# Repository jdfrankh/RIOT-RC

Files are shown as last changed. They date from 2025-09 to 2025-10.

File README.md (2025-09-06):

### RIOT-RC
This library contains hardware and software files for Robo RIOT's Rc controllers. These sets are meant to control 1lb, 3lb, and possibly 5lb robotics in a compact package, allowing any individual to easily create their own open-source battle bot electronics set.  

## Quickstart -- Preassembled Remote and Receiver

The RIOT RC has the following basic specs

# Receiver
| Parameter | Value |
|---|---|
| Supply Voltage  | 5V - 36V  |
| Idle Amperage Time  | .05A  |
| Default ESC Hookups | 2 |
| Default Servo Hookups | 2 |
| DC Drives | 2 |

# Remote 
| Parameter | Value |
|---|---|
| Operating Time | ~3 hours  |
| Radio Range  | ~40-60m  |
| Analog Joysticks | 2 |
| Buttons | 4 |

# Hookup

The pinout of the Receiver is the following:

Screenshot 2025-09-06 at 12 33 19 AM

Attach your receiver as according to the diagram:

Screenshot 2025-09-06 at 1 02 53 AM

# Basic Operation

The staring operation of the remote goes as such.

1. Start your remote
2. Select your desired reciever by username
3. Control your reciever

The controls for selecting your receiver go as such:

Screenshot 2025-09-06 at 1 23 56 AM

The OLED screen will display all **Powered** receivers automatically with their assigned name. Select one to automatically connect it. 

The controls for the remote after the reciver go as such: 

Screenshot 2025-09-06 at 1 29 56 AM

Keep in mind that there is a **Software** based arming mechanism for the BLDC motor. The receiver will not activate it unless the arming command is first sent. It may take about 5 seconds to arm your receiver. **Please be cautious when actiavate the BLDC, as it's speed rating may be enough to harm.**

The brushed motors are programmed to act as a drive, moving according to a two wheeled battlebot. Although the supply voltage is attached to the motor drive, the original code is deisgned around a 6V N20, and thus creates a PWM signal to prevent users from frying the motor. To change this. Please refer to the **Change code** section for more information.

## Simple edits - Uploading Sketches

Many values as of right now are hard-coded into the remote or receiver to change, and most of those changes can be altered by re-flashing them. The software was created in PlatoformIO, and integrated IDE into VSCode for microcontrollers. Many resources are avaliable for you to download and operate the software.

Once PlatformIO has been downloaded, clone the repository and naviage to /RIOT-RC/PlatformIO Imports/ and select the platoformIO directory. 

**Caution**: The receiver is attached to the battery voltage. **FOR THE RECEIVER DO NOT ATTACH A USB WHILE A LIPO BATTERY IS ATTACHED. YOU WILL FRY YOUR USB PORT AND YOUR COMPUTER**

Most easily accessible commands will be placed at the top of main.cpp for ease of access. Alterations from the basic control scheme will be implemented later. 

Screenshot 2025-09-06 at 1 55 30 AM

# Battery Charging

The Remote has a one cell battery charger. Simply attach the charger to your USB to recharge it.

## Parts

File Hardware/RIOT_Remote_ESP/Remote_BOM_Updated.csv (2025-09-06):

Value | Reference | Footprint | Digikey Link to Item | Qty
MCP73831-2-OT | U9 | Package_TO_SOT_SMD:SOT-23-5 | https://www.digikey.com/en/products/filter/battery-chargers/781?s=N4IgTCBcDaILIGEAKB2AzADjQRhAXQF8g | 1
ASV-40MHz | X1 | Oscillator:Oscillator_SMD_Abracon_ASE-4Pin_3.2x2.5mm_HandSoldering | https://www.digikey.com/en/products/detail/kyocera-avx/CX3225SA40000D0PTWCC/9698138 | 1
TPS63031DSK | U3 | Package_SON:WSON-10-1EP_2.5x2.5mm_P0.5mm_EP1.2x2mm | https://www.digikey.com/en/products/detail/texas-instruments/TPS63031DSKR/2048021 | 1
ESP32-C3FH | U1 | Package_DFN_QFN:QFN-32-1EP_5x5mm_P0.5mm_EP3.7x3.7mm | https://www.digikey.com/en/products/detail/espressif-systems/ESP32-C3FH4X/24366489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 | 1
SM6T10A | D1 | Diode_SMD:D_SMB | https://www.digikey.com/en/products/detail/stmicroelectronics/SM6T10A/1039070 | 1
USB_C_Receptacle_USB2.0_16P | J2 | Connector_USB:USB_C_Receptacle_GCT_USB4085 | https://www.digikey.com/en/products/detail/gct/USB4085-GF-A/9859662?s=N4IgTCBcDaIK4GcBGAWADADgKwgLoF8g | 1
Antenna_Shield | AE1 | Connector_Coaxial:U.FL_Molex_MCRF_73412-0110_Vertical | https://www.digikey.com/en/products/detail/hirose-electric-co-ltd/U-FL-R-SMT-1-60/4285475 | 1
12pF | C1,C2 | Capacitor_SMD:C_0402_1005Metric_Pad0.74x0.62mm_HandSolder |  | 2
10uF | C3,C27,C28,C29 | Capacitor_SMD:C_0603_1608Metric_Pad1.08x0.95mm_HandSolder,Capacitor_SMD:C_1206_3216Metric_Pad1.33x1.80mm_HandSolder |  | 4
1uF | C5,C8,C24 | Capacitor_SMD:C_0402_1005Metric_Pad0.74x0.62mm_HandSolder |  | 3
1p2 | C11 | Capacitor_SMD:C_0402_1005Metric_Pad0.74x0.62mm_HandSolder |  | 1
100uF | C13 | Capacitor_SMD:CP_Elec_4x5.4 |  | 1
100nF | C14,C23,C21,C22,C4,C6,C7,C26 | Capacitor_SMD:C_0402_1005Metric_Pad0.74x0.62mm_HandSolder |  | 8
1p6 | C15 | Capacitor_SMD:C_0402_1005Metric_Pad0.74x0.62mm_HandSolder |  | 1
10nF | C16 | Capacitor_SMD:C_0402_1005Metric_Pad0.74x0.62mm_HandSolder |  | 1
4.7uF | C25 | Capacitor_SMD:C_0402_1005Metric_Pad0.74x0.62mm_HandSolder |  | 1
YELLOW | D2 | LED_SMD:LED_1206_3216Metric_Pad1.42x1.75mm_HandSolder |  | 1
24nH | L1 | Inductor_SMD:L_0603_1608Metric_Pad1.05x0.95mm_HandSolder |  | 1
2 nH | L2 | Inductor_SMD:L_0603_1608Metric_Pad1.05x0.95mm_HandSolder |  | 1
2n2 | L3,L4 | Inductor_SMD:L_0603_1608Metric_Pad1.05x0.95mm_HandSolder |  | 2
1.5uH | L5 | Inductor_SMD:L_Coilcraft_LPS3010 |  | 1
470 | R2 | Resistor_SMD:R_0402_1005Metric_Pad0.72x0.64mm_HandSolder |  | 1
2k | R3 | Resistor_SMD:R_0402_1005Metric_Pad0.72x0.64mm_HandSolder |  | 1
10k | R4 | Resistor_SMD:R_0402_1005Metric_Pad0.72x0.64mm_HandSolder |  | 1
5.1k | R14,R15,R5,R6,R7,R8,R12,R13 | Resistor_SMD:R_0402_1005Metric_Pad0.72x0.64mm_HandSolder |  | 8

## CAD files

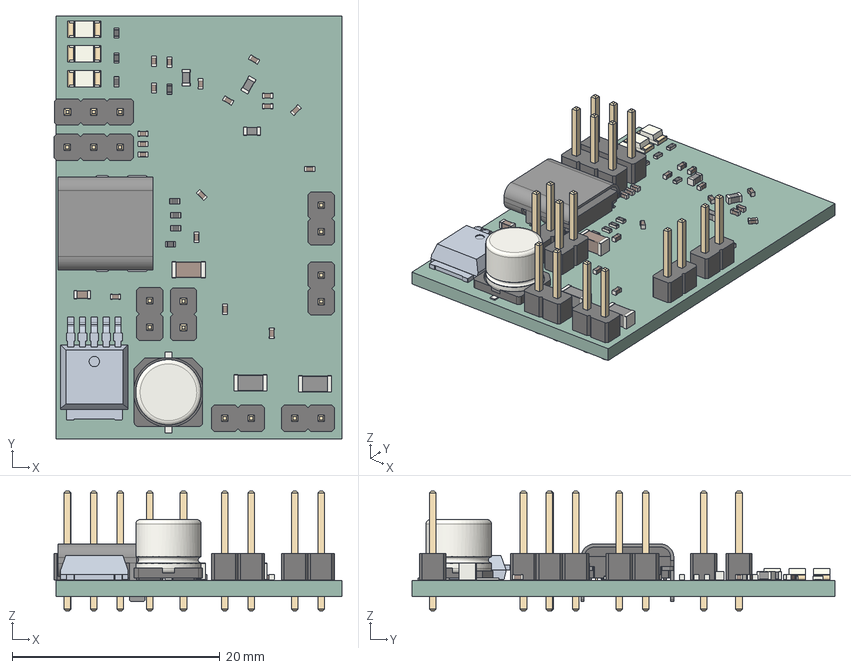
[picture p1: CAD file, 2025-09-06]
CAD/RIOT_Receiver_ESP.step
27.7 x 40.7 x 11.5 mm
PinHeader_1x02_P2.54mm_Vertical x 6
R_0402_1005Metric x 8
LED_1206_3216Metric x 3
C_0402_1005Metric x 18
L_0603_1608Metric x 3
PinHeader_1x03_P2.54mm_Vertical x 2
L_1206_3216Metric x 2
C_Elec_6.3x5.8
C_1206_3216Metric
USB_C_Receptacle_GCT_USB4085
RIOT_Receiver_ESP 1.40.1
C_0603_1608Metric
RIOT_Receiver_ESP_PCB

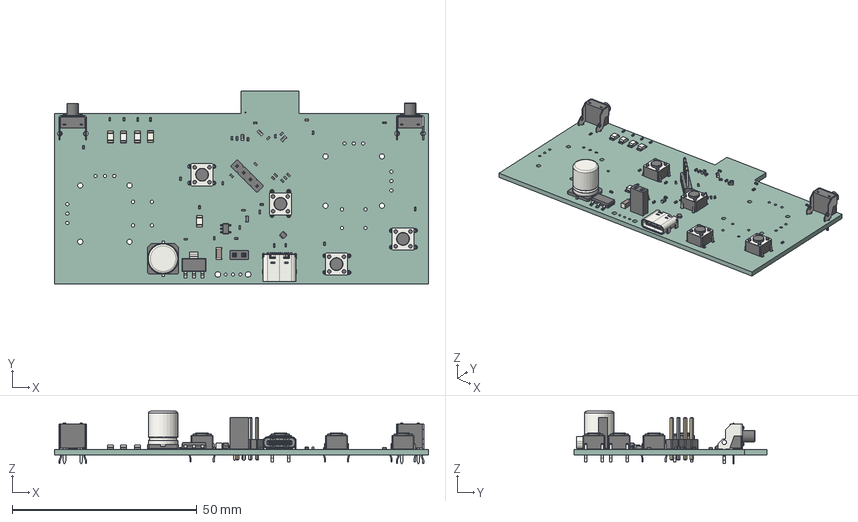
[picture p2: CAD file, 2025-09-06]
Hardware/RIOT_Remote_ESP/RIOT_Remote_ESP.step
101.1 x 52.1 x 14.2 mm
R_0402_1005Metric x 13
USB_C_Receptacle_GCT_USB4105-xx-A_16P_TopMnt_Horizontal
C_0402_1005Metric x 23
L_0603_1608Metric x 4
SOT-666
SW_PUSH_6mm_H4.3mm x 4
LED_1206_3216Metric x 5
PinSocket_1x02_P2.54mm_Vertical
SW_Tactile_SPST_Angled_PTS645Vx58-2LFS x 2
SOT-23-5
C_Elec_8x10.2
SOT-223
C_1206_3216Metric
PinHeader_1x04_P2.54mm_Vertical
RIOT_Remote_ESP_PCB

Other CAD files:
CAD/ESPController v23.f3z

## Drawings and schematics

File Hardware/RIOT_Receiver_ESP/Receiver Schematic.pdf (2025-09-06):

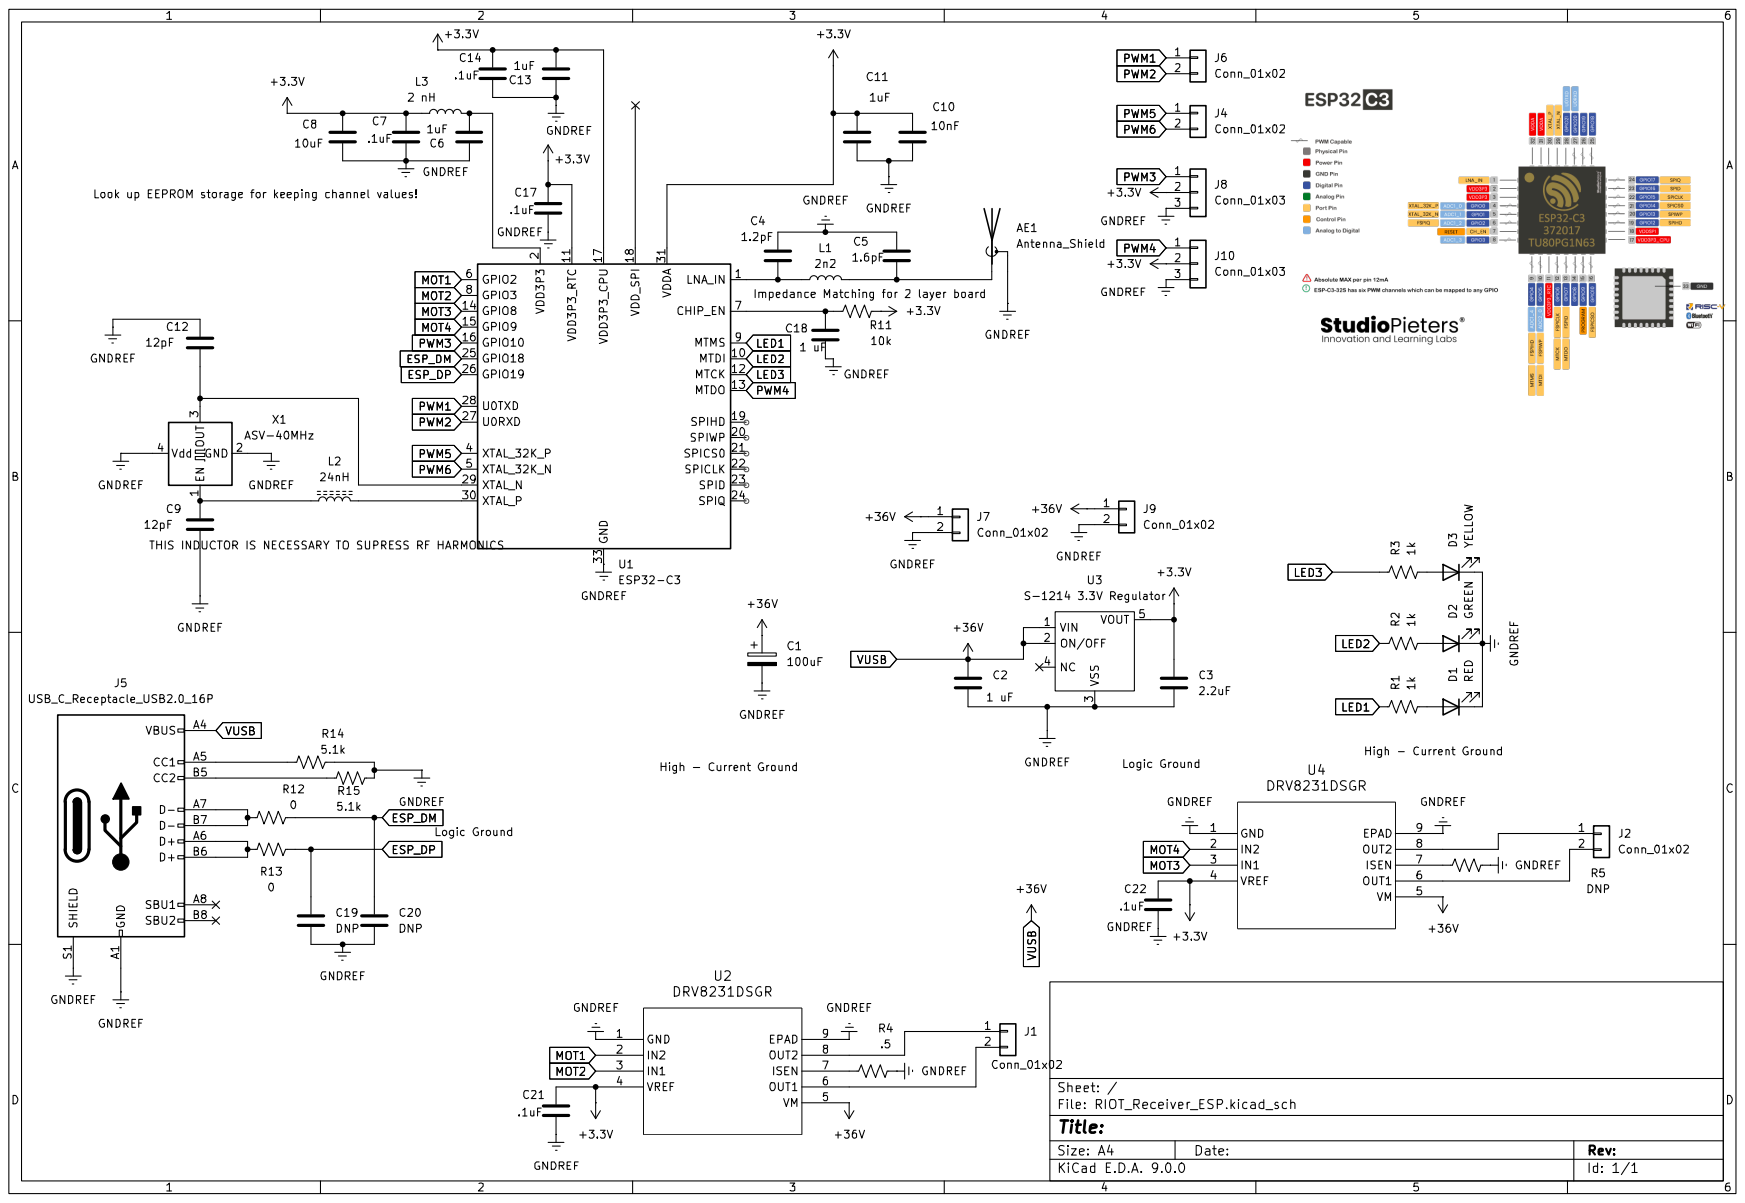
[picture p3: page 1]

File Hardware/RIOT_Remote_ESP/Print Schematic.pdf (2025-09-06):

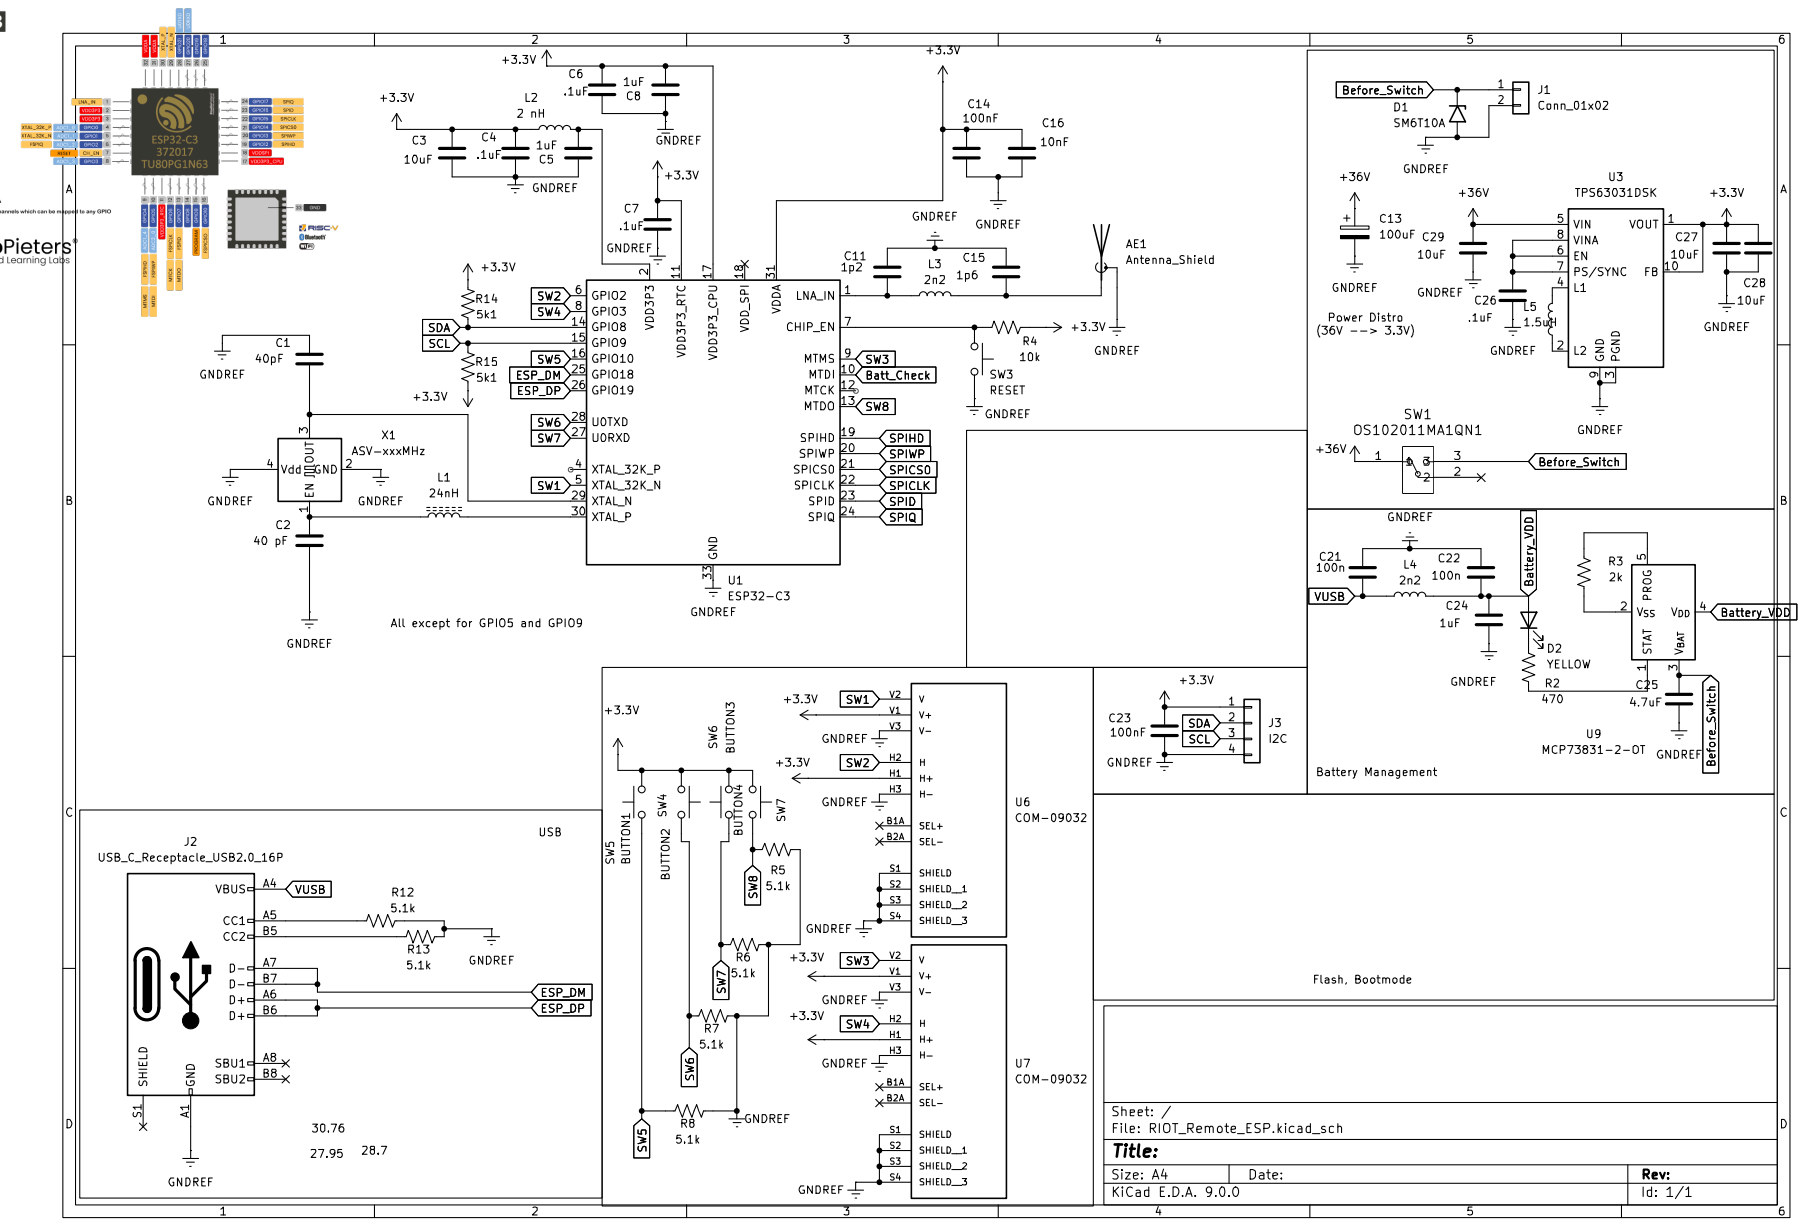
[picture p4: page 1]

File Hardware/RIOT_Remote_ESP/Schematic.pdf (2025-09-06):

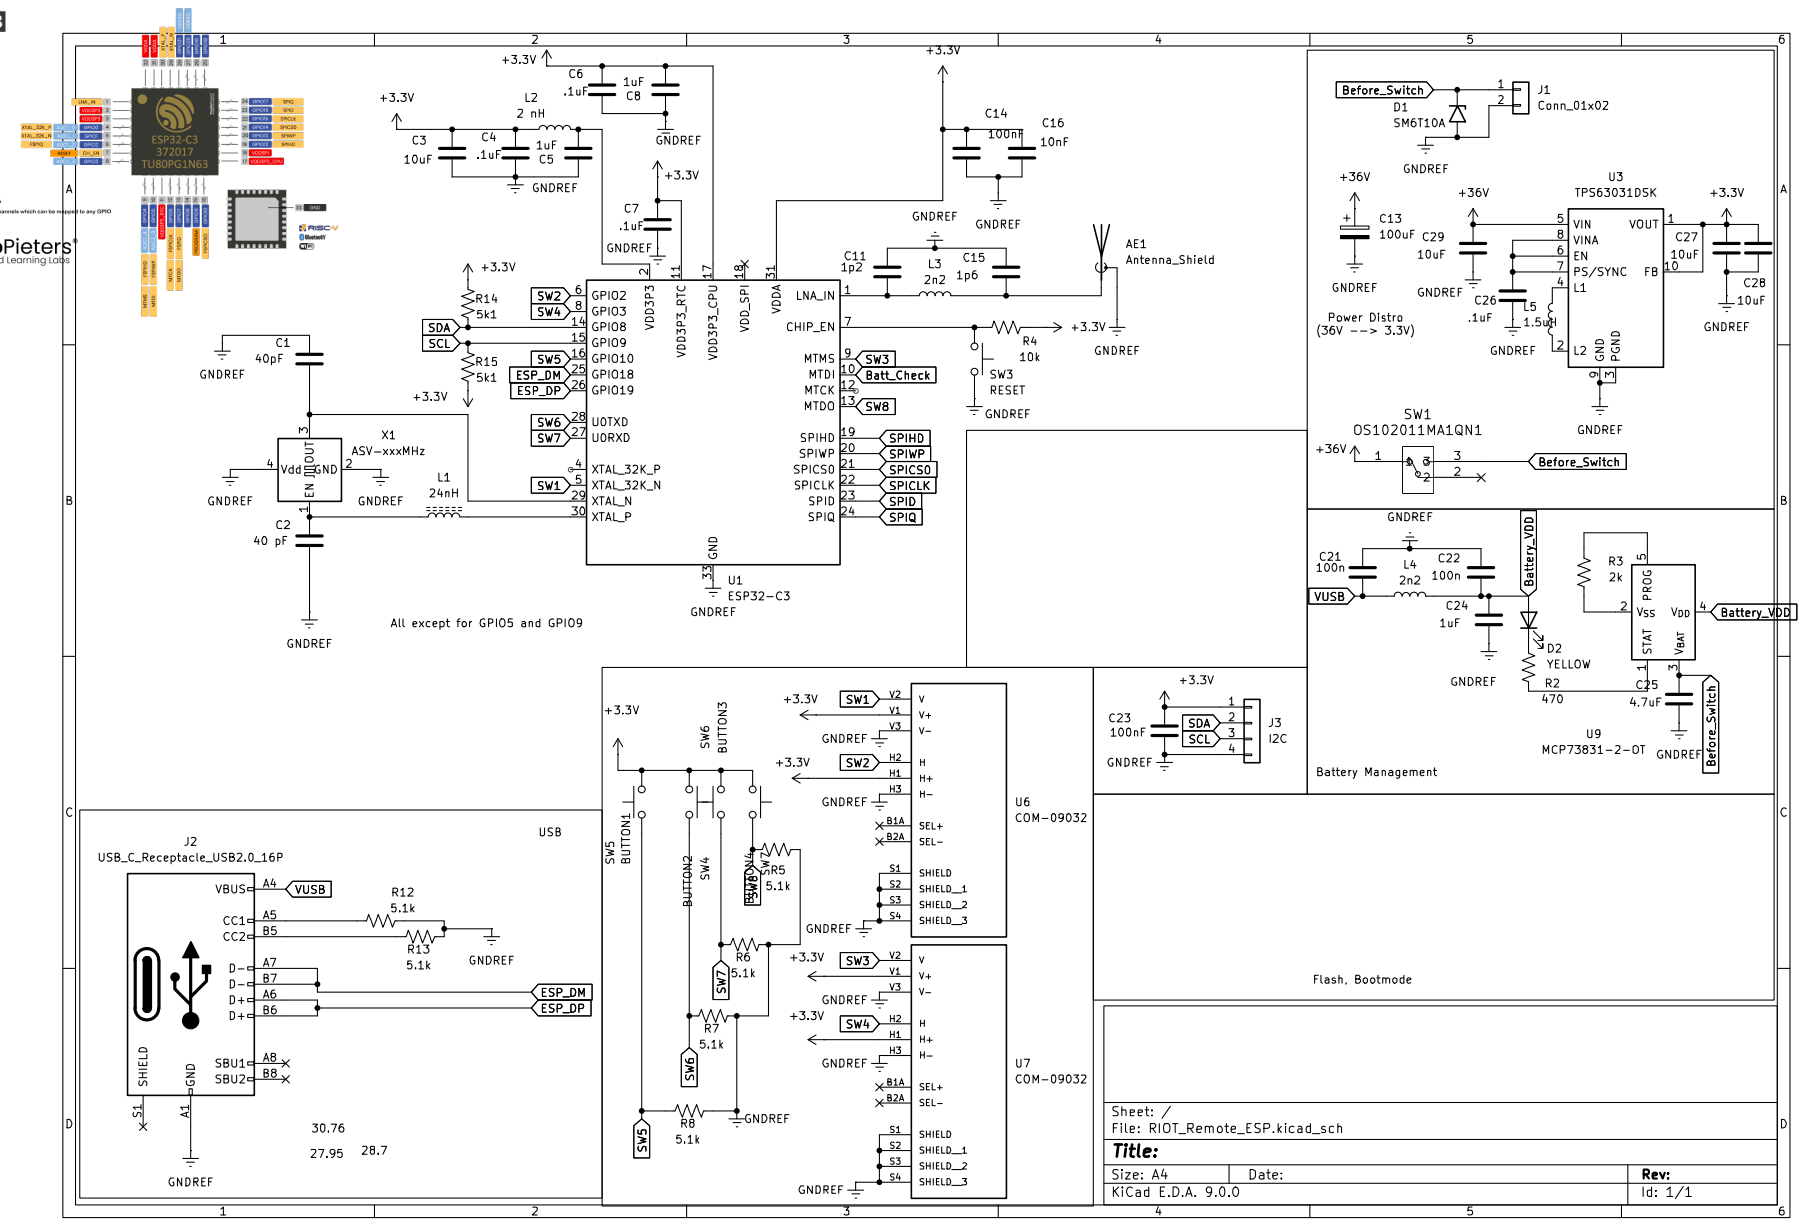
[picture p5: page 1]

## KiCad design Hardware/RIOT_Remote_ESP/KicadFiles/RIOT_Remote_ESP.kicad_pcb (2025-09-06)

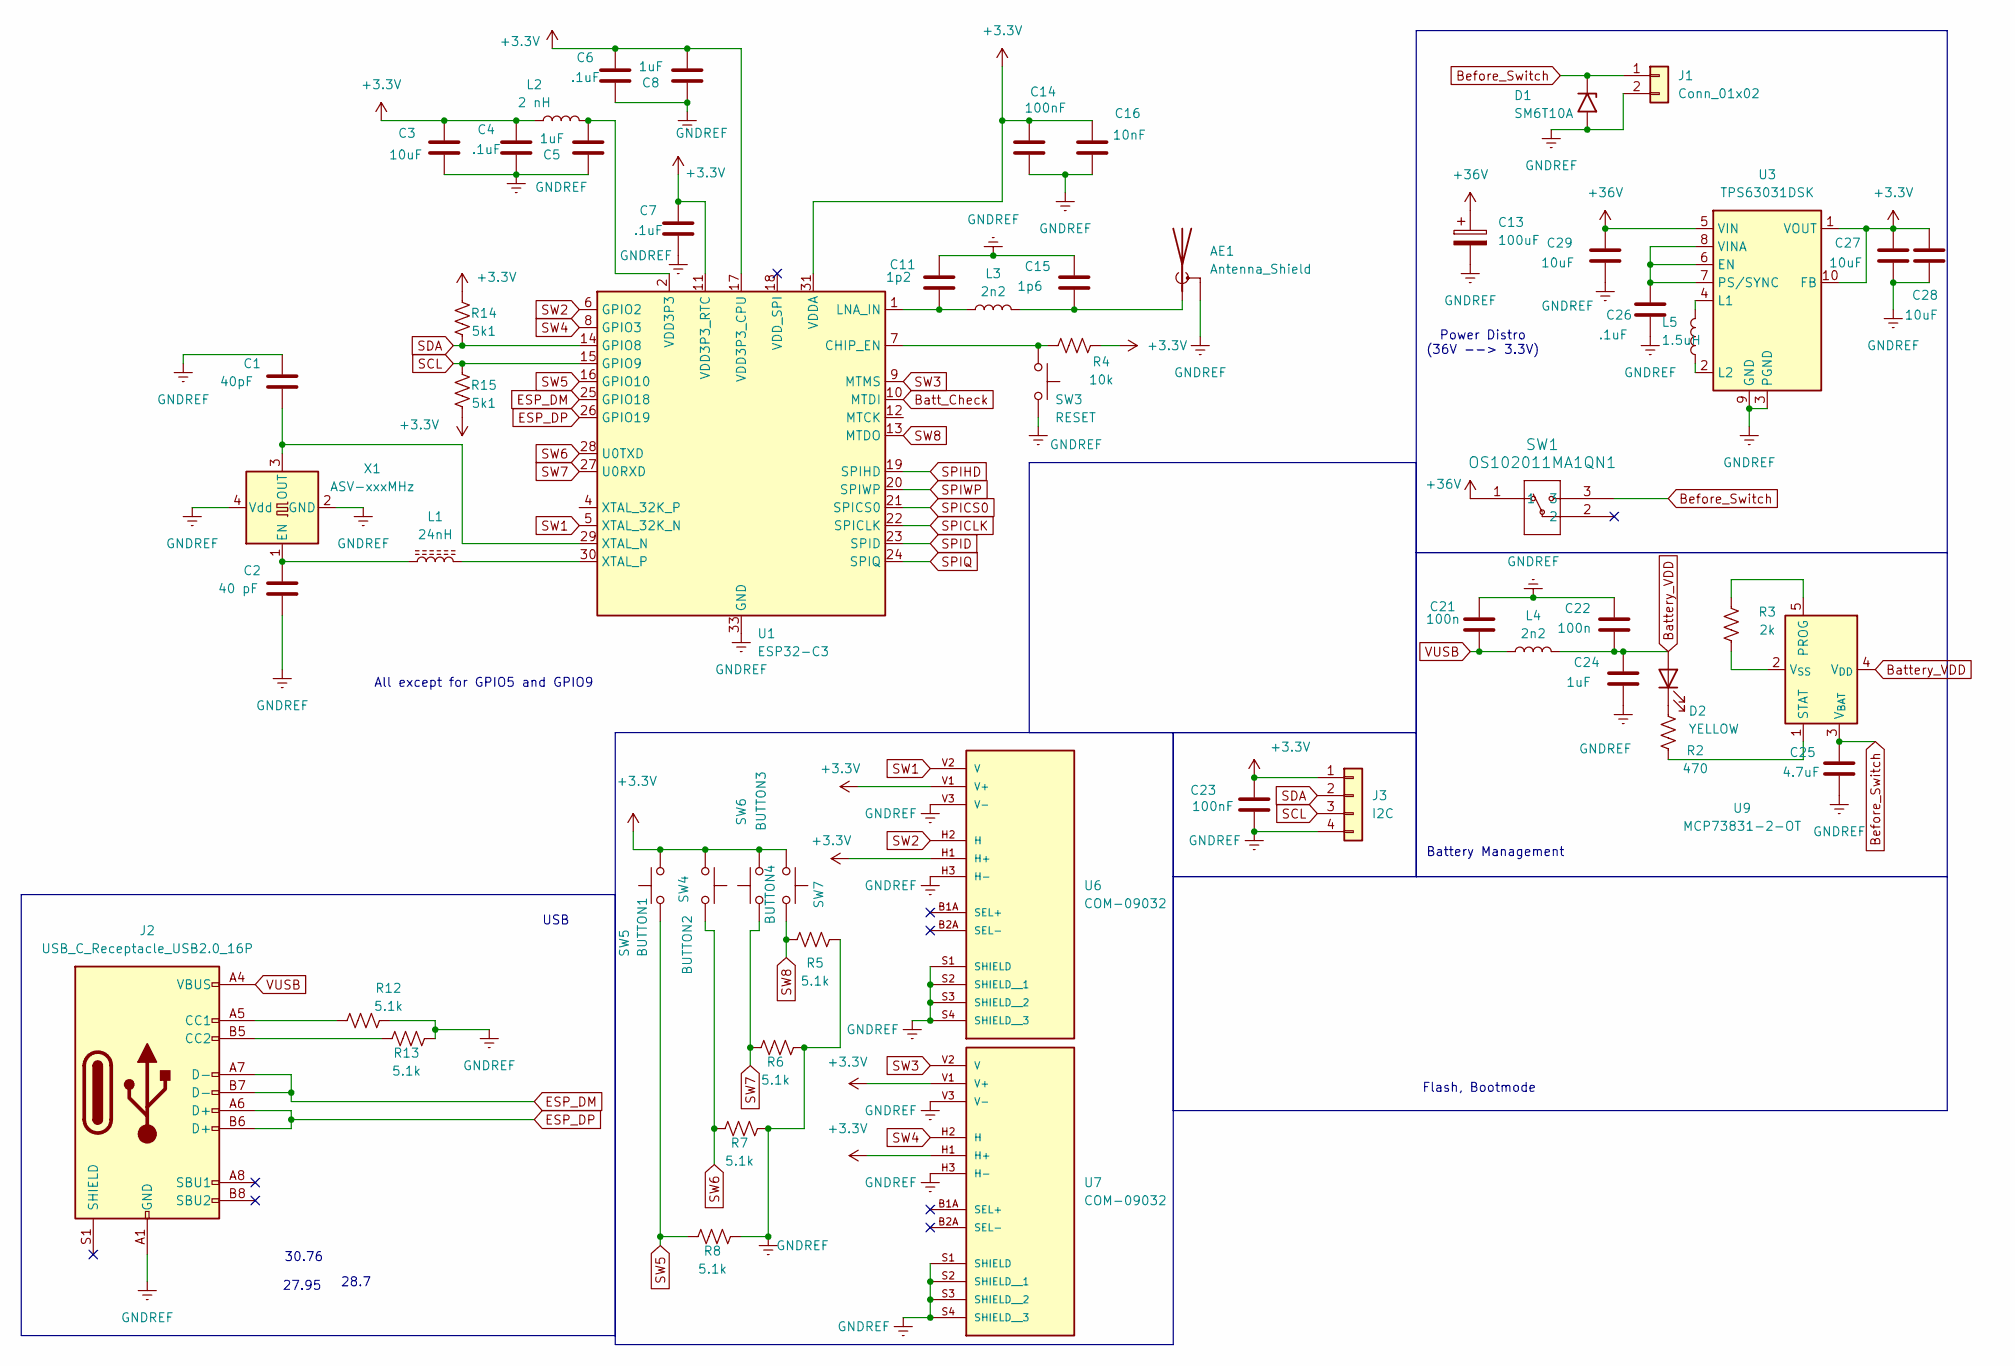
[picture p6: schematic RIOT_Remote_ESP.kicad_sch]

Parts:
AE1: Antenna_Shield; U.FL_Molex_MCRF_73412-0110_Vertical
C1: 40pF; C_0402_1005Metric_Pad0.74x0.62mm_HandSolder
C2: 40 pF; C_0402_1005Metric_Pad0.74x0.62mm_HandSolder
C3: 10uF; C_1206_3216Metric_Pad1.33x1.80mm_HandSolder
C4, C6, C7, C26: .1uF; C_0402_1005Metric_Pad0.74x0.62mm_HandSolder
C5, C8, C24: 1uF; C_0402_1005Metric_Pad0.74x0.62mm_HandSolder
C11: 1p2; C_0402_1005Metric_Pad0.74x0.62mm_HandSolder
C13: 100uF; CP_Elec_4x5.4
C14, C23: 100nF; C_0402_1005Metric_Pad0.74x0.62mm_HandSolder
C15: 1p6; C_0402_1005Metric_Pad0.74x0.62mm_HandSolder
C16: 10nF; C_0402_1005Metric_Pad0.74x0.62mm_HandSolder
C21, C22: 100n; C_0402_1005Metric_Pad0.74x0.62mm_HandSolder
C25: 4.7uF; C_0402_1005Metric_Pad0.74x0.62mm_HandSolder
C27, C28, C29: 10uF; C_0603_1608Metric_Pad1.08x0.95mm_HandSolder
D1: SM6T10A; D_SMB
D2: YELLOW; LED_1206_3216Metric_Pad1.42x1.75mm_HandSolder
J1: Conn_01x02; PinSocket_1x02_P2.54mm_Vertical
J2: USB_C_Receptacle_USB2.0_16P; USB_C_Receptacle_GCT_USB4085
J3: I2C; PinHeader_1x04_P2.54mm_Vertical
L1: 24nH; L_0603_1608Metric_Pad1.05x0.95mm_HandSolder
L2: 2 nH; L_0603_1608Metric_Pad1.05x0.95mm_HandSolder
L3, L4: 2n2; L_0603_1608Metric_Pad1.05x0.95mm_HandSolder
L5: 1.5uH; L_Coilcraft_LPS3010
R2: 470; R_0402_1005Metric_Pad0.72x0.64mm_HandSolder
R3: 2k; R_0402_1005Metric_Pad0.72x0.64mm_HandSolder
R4: 10k; R_0402_1005Metric_Pad0.72x0.64mm_HandSolder
R5, R6, R7, R8, R12, R13: 5.1k; R_0402_1005Metric_Pad0.72x0.64mm_HandSolder
R14, R15: 5k1; R_0402_1005Metric_Pad0.72x0.64mm_HandSolder
SW1: OS102011MA1QN1; OS102011MA1QN1_CNK
SW3: RESET; SW_PUSH_6mm_H4.3mm
SW4: BUTTON2; SW_Tactile_SPST_Angled_PTS645Vx58-2LFS
SW5: BUTTON1; SW_PUSH_6mm_H4.3mm
SW6: BUTTON3; SW_PUSH_6mm_H4.3mm
SW7: BUTTON4; SW_Tactile_SPST_Angled_PTS645Vx58-2LFS
U1: ESP32-C3; QFN-32-1EP_5x5mm_P0.5mm_EP3.7x3.7mm
U3: TPS63031DSK; WSON-10-1EP_2.5x2.5mm_P0.5mm_EP1.2x2mm
U6, U7: COM-09032; XDCR_COM-09032; PARTREV N/A
U9: MCP73831-2-OT; SOT-23-5
X1: ASV-xxxMHz; Oscillator_SMD_Abracon_ASE-4Pin_3.2x2.5mm_HandSoldering

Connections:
+3.3V: C3.1, C4.1, C6.1, C7.1, C8.2, C14.1, C16.1, C23.1, C27.1, C28.1, J3.1, L2.1, R4.2, R14.2, R15.1, SW4.1, SW5.2, SW6.2, SW7.1, U1.11 (VDD3P3_RTC), U1.17 (VDD3P3_CPU), U1.31 (VDDA), U1.32 (VDDA), U3.1 (VOUT), U3.10 (FB), U6.H1 (H+), U6.V1 (V+), U7.H1 (H+), U7.V1 (V+)
+36V: C13.1, C29.1, SW1.1, U3.5 (VIN); also elsewhere on the board
Batt_Check: U1.10 (MTDI)
Battery_VDD: C22.2, C24.1, D2.2 (A), L4.2, U9.4 (V_{DD})
Before_Switch: C25.1, D1.1 (A1), J1.1, SW1.3, U9.3 (V_{BAT}); also elsewhere on the board
ESP_DM: J2.A7 (D-), J2.B7 (D-), U1.25 (GPIO18)
ESP_DP: J2.A6 (D+), J2.B6 (D+), U1.26 (GPIO19)
GNDREF: AE1.2 (Shield), C1.1, C2.2, C3.2, C4.2, C5.1, C6.2, C7.2, C8.1, C11.1, C13.2, C14.2, C15.1, C16.2, C21.1, C22.1, C23.2, C24.2, C25.2, C26.2, C27.2, C28.2, C29.2, D1.2 (A2), J1.2, J2.A1 (GND), J2.A12 (GND), J2.B1 (GND), J2.B12 (GND), J3.4, R5.2, R6.2, R7.2, R8.2, R12.2, R13.2, SW3.2, U1.33 (GND), U3.3 (PGND), U3.9 (GND), U3.11 (PGND), U6.H3 (H-), U6.S1 (SHIELD), U6.S2 (SHIELD__1), U6.S3 (SHIELD__2), U6.S4 (SHIELD__3), U6.V3 (V-), U7.H3 (H-), U7.S1 (SHIELD), U7.S2 (SHIELD__1), U7.S3 (SHIELD__2), U7.S4 (SHIELD__3), U7.V3 (V-), X1.2 (GND), X1.4 (Vdd); also elsewhere on the board
unnamed: AE1.1 (A), C15.2, L3.2
unnamed: C5.2, L2.2, U1.2 (VDD3P3), U1.3 (VDD3P3)
unnamed: D2.1 (K), R2.2
unnamed: J2.A5 (CC1), R12.1
unnamed: J2.B5 (CC2), R13.1
unnamed: R4.1, SW3.1, U1.7 (CHIP_EN)
unnamed: C11.2, L3.1, U1.1 (LNA_IN)
unnamed: C1.2, U1.29 (XTAL_N), X1.3 (OUT)
unnamed: L1.2, U1.30 (XTAL_P)
unnamed: C26.1, U3.6 (EN), U3.7 (PS/SYNC), U3.8 (VINA)
unnamed: L5.2, U3.4 (L1)
unnamed: L5.1, U3.2 (L2)
unnamed: R3.2, U9.5 (PROG)
unnamed: R2.1, U9.1 (STAT)
unnamed: R3.1, U9.2 (V_{SS})
unnamed: C2.1, L1.1, X1.1 (EN)
SCL: J3.3, R15.2, U1.15 (GPIO9)
SDA: J3.2, R14.1, U1.14 (GPIO8)
SPICLK: U1.22 (SPICLK)
SPICS0: U1.21 (SPICS0)
SPID: U1.23 (SPID)
SPIHD: U1.19 (SPIHD)
SPIQ: U1.24 (SPIQ)
SPIWP: U1.20 (SPIWP)
SW1: U1.5 (XTAL_32K_N), U6.V2 (V)
SW2: U1.6 (GPIO2), U6.H2 (H)
SW3: U1.9 (MTMS), U7.V2 (V)
SW4: U1.8 (GPIO3), U7.H2 (H)
SW5: R8.1, SW5.1, U1.16 (GPIO10)
SW6: R7.1, SW4.2, U1.28 (U0TXD)
SW7: R6.1, SW6.1, U1.27 (U0RXD)
SW8: R5.1, SW7.2, U1.13 (MTDO)
VUSB: C21.2, J2.A4 (VBUS), J2.A9 (VBUS), J2.B4 (VBUS), J2.B9 (VBUS), L4.1

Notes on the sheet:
28.7
Battery Management
Power Distro (36V --> 3.3V)
Flash, Bootmode
27.95
All except for GPIO5 and GPIO9
USB
30.76

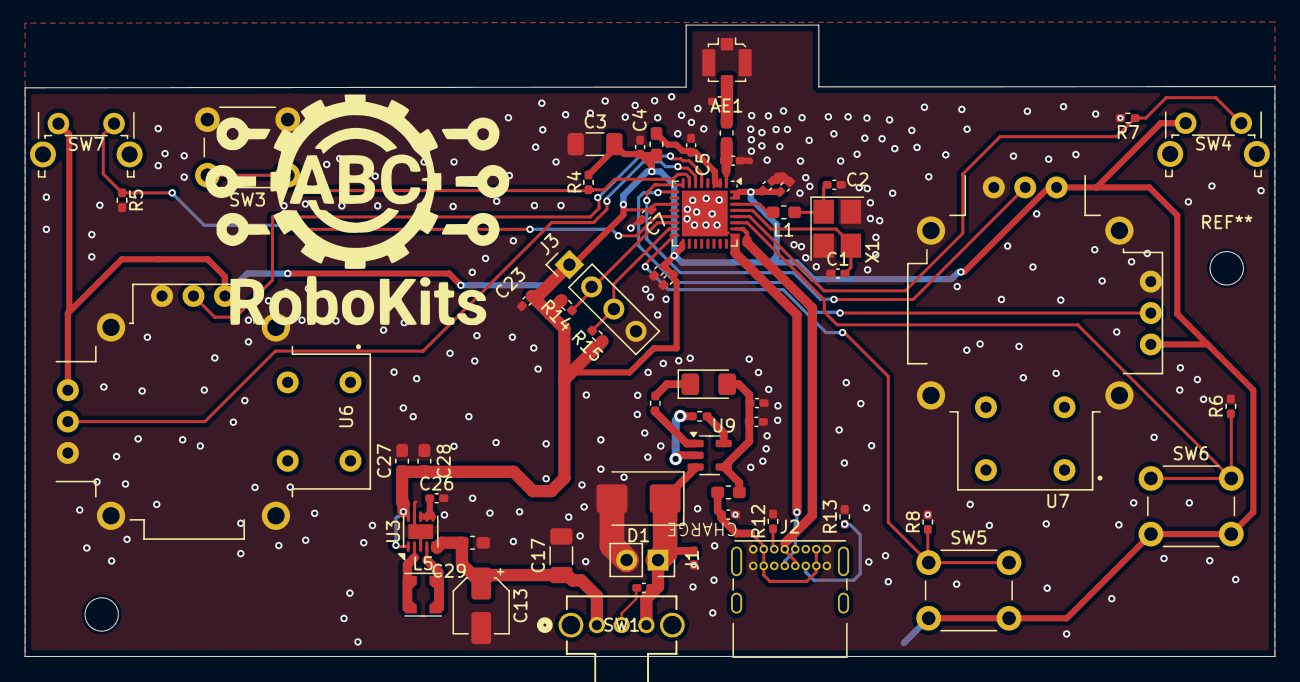
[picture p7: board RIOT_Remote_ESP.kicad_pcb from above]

Board: 2 copper layers, 101.1 x 51.1 mm, 58 parts (0 on the bottom side), 34 nets.

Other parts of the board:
C17: 1 uF; C_1206_3216Metric_Pad1.33x1.80mm_HandSolder
C25#2: 4.7uF; C_0402_1005Metric_Pad0.74x0.62mm_HandSolder

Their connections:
+36V: C17.1; also elsewhere on the board
Before_Switch: C25#2.1; also elsewhere on the board
GNDREF: C17.2, C25#2.2; also elsewhere on the board

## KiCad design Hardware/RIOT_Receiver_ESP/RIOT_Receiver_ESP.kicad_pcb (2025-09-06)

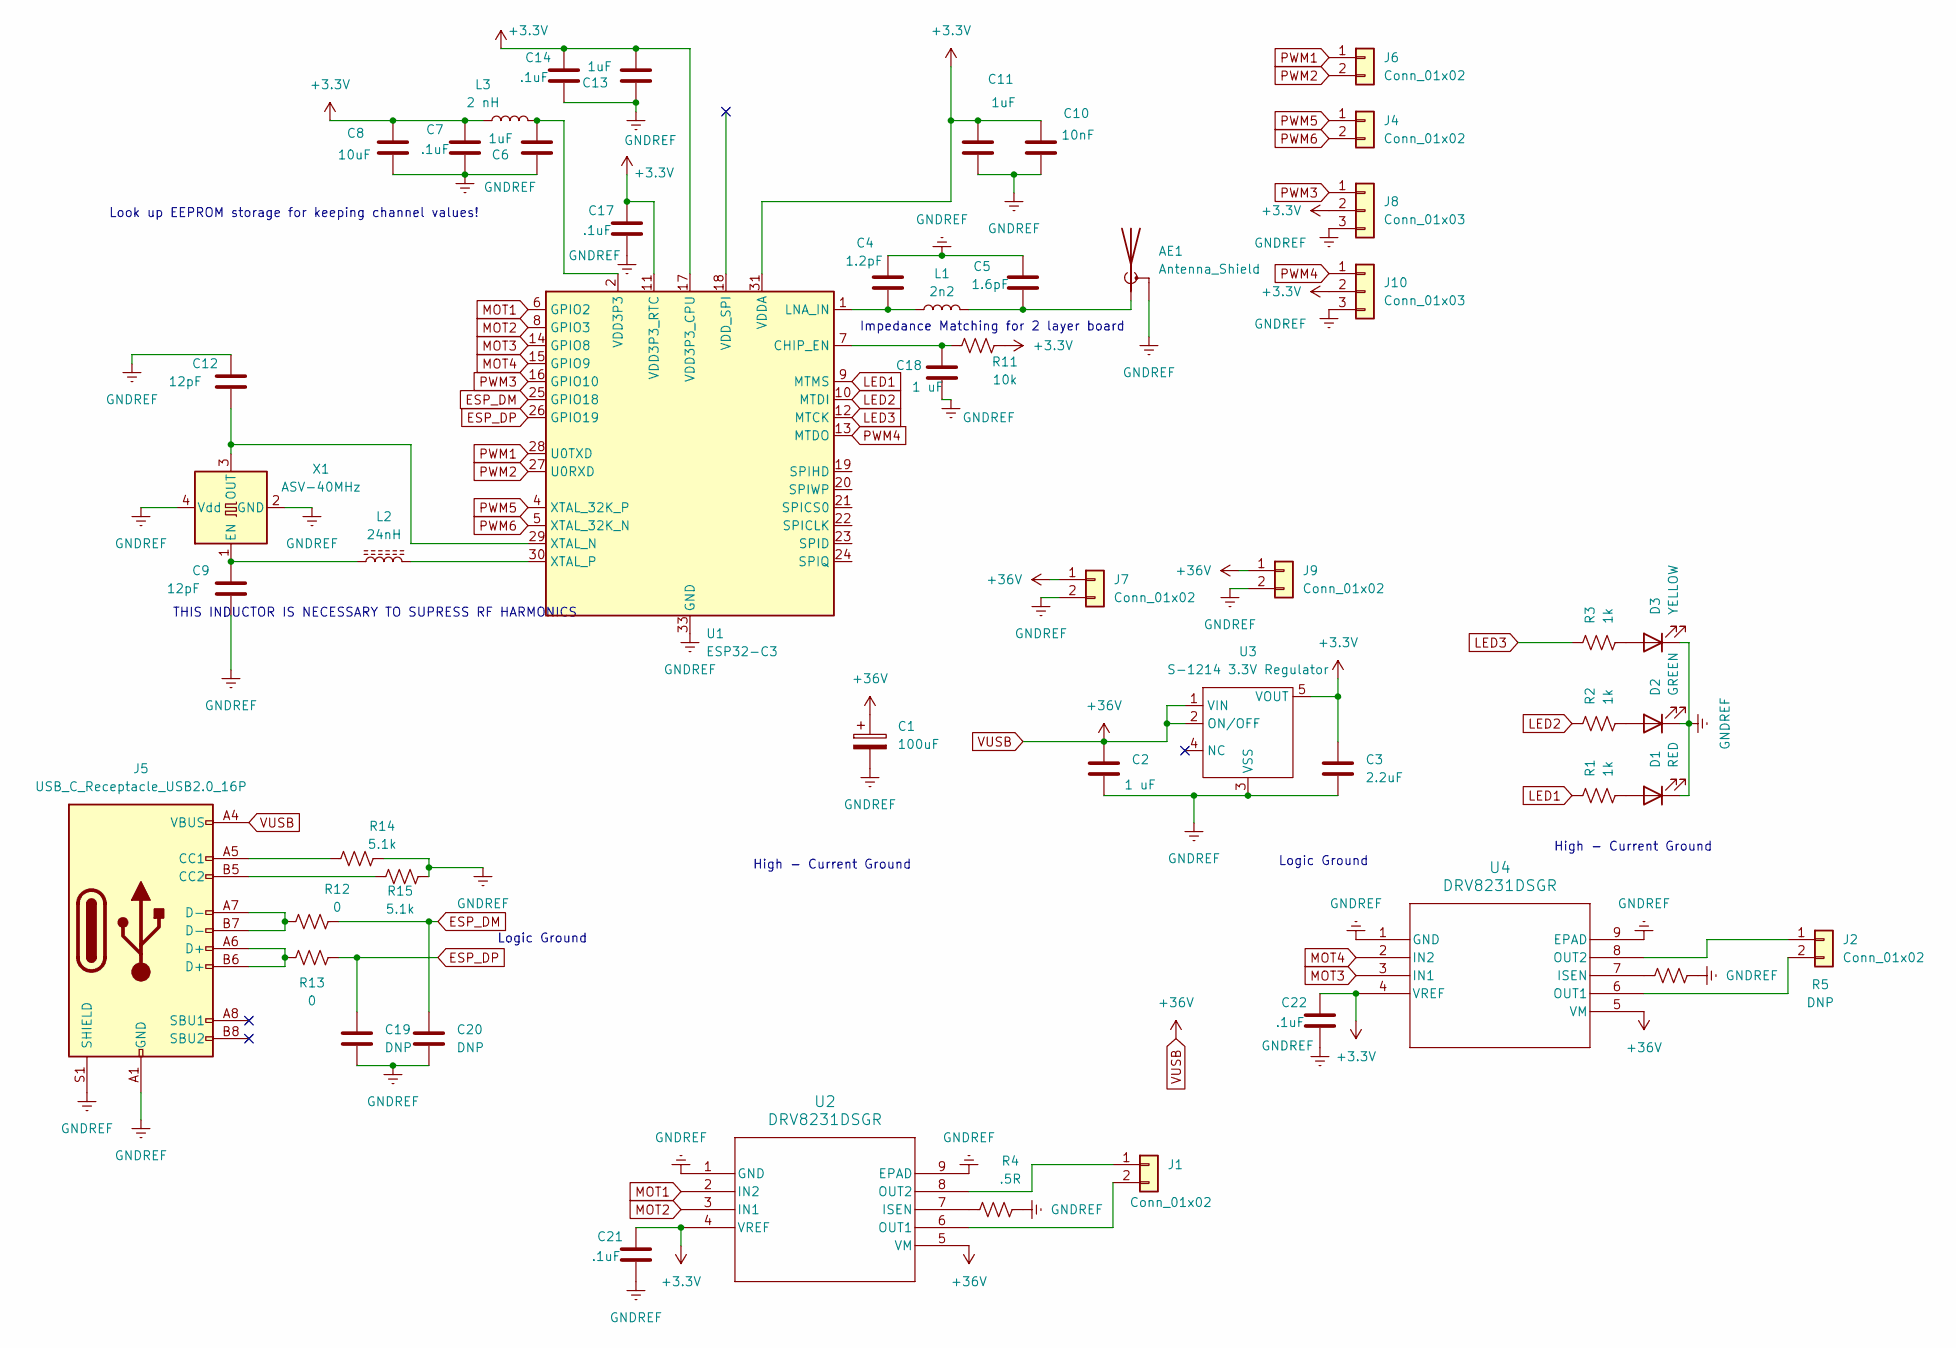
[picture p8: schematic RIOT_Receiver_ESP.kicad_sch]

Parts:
AE1: Antenna_Shield
C1: 100uF; C_Elec_8x10.2
C2, C18: 1 uF; C_0402_1005Metric_Pad0.74x0.62mm_HandSolder
C3: 2.2uF; C_0603_1608Metric_Pad1.08x0.95mm_HandSolder
C4: 1.2pF; C_0402_1005Metric_Pad0.74x0.62mm_HandSolder
C5: 1.6pF; C_0402_1005Metric_Pad0.74x0.62mm_HandSolder
C6, C11, C13: 1uF; C_0402_1005Metric_Pad0.74x0.62mm_HandSolder
C7, C14, C17, C21, C22: .1uF; C_0402_1005Metric_Pad0.74x0.62mm_HandSolder
C8: 10uF; C_0402_1005Metric_Pad0.74x0.62mm_HandSolder
C9, C12: 12pF; C_0402_1005Metric_Pad0.74x0.62mm_HandSolder
C10: 10nF; C_0402_1005Metric_Pad0.74x0.62mm_HandSolder
C19, C20: DNP; C_0402_1005Metric_Pad0.74x0.62mm_HandSolder
D1: RED; LED_1206_3216Metric_Pad1.42x1.75mm_HandSolder
D2: GREEN; LED_1206_3216Metric_Pad1.42x1.75mm_HandSolder
D3: YELLOW; LED_1206_3216Metric_Pad1.42x1.75mm_HandSolder
J1, J2, J4, J6, J7, J9: Conn_01x02; PinHeader_1x02_P2.54mm_Vertical
J5: USB_C_Receptacle_USB2.0_16P; USB_C_Receptacle_GCT_USB4085
J8, J10: Conn_01x03; PinHeader_1x03_P2.54mm_Vertical
L1: 2n2; L_0603_1608Metric_Pad1.05x0.95mm_HandSolder
L2: 24nH; L_0603_1608Metric_Pad1.05x0.95mm_HandSolder
L3: 2 nH; L_0603_1608Metric_Pad1.05x0.95mm_HandSolder
R1, R2, R3: 1k; R_0402_1005Metric_Pad0.72x0.64mm_HandSolder
R4: .5R; L_1206_3216Metric_Pad1.22x1.90mm_HandSolder
R5: DNP; L_1206_3216Metric_Pad1.22x1.90mm_HandSolder
R11: 10k; R_0402_1005Metric_Pad0.72x0.64mm_HandSolder
R12, R13: 0; R_0402_1005Metric_Pad0.72x0.64mm_HandSolder
R14, R15: 5.1k; R_0402_1005Metric_Pad0.72x0.64mm_HandSolder
U1: ESP32-C3; QFN-32-1EP_5x5mm_P0.5mm_EP3.7x3.7mm
U2, U4: DRV8231DSGR; WSON8_DRV8231_TEX
U3: S-1214 3.3V Regulator; TO-252-5_TabPin3
X1: ASV-40MHz; Oscillator_SMD_Abracon_ASE-4Pin_3.2x2.5mm

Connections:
+3.3V: C3.1, C7.1, C8.1, C10.1, C11.1, C13.2, C14.1, C17.1, C21.1, C22.1, J8.2, J10.2, L3.1, R11.2, U1.11 (VDD3P3_RTC), U1.17 (VDD3P3_CPU), U1.31 (VDDA), U1.32 (VDDA), U2.4 (VREF), U3.5 (VOUT), U4.4 (VREF)
ESP_DM: C20.1, R12.2, U1.25 (GPIO18)
ESP_DP: C19.1, R13.1, U1.26 (GPIO19)
GNDREF: AE1.2 (Shield), C1.2, C2.2, C3.2, C4.1, C5.1, C6.1, C7.2, C8.2, C9.2, C10.2, C11.2, C12.1, C13.1, C14.2, C17.2, C18.2, C19.2, C20.2, C21.2, C22.2, D1.1 (K), D2.1 (K), D3.1 (K), J5.A1 (GND), J5.A12 (GND), J5.B1 (GND), J5.B12 (GND), J5.S1 (SHIELD), J7.2, J8.3, J9.2, J10.3, R4.2, R5.2, R14.2, R15.2, U1.33 (GND), U2.1 (GND), U2.9 (EPAD), U3.3 (VSS), U4.1 (GND), U4.9 (EPAD), X1.2 (GND), X1.4 (Vdd)
LED1: R1.1, U1.9 (MTMS)
LED2: R2.1, U1.10 (MTDI)
LED3: R3.1, U1.12 (MTCK)
MOT1: U1.6 (GPIO2), U2.2 (IN2)
MOT2: U1.8 (GPIO3), U2.3 (IN1)
MOT3: U1.14 (GPIO8), U4.3 (IN1)
MOT4: U1.15 (GPIO9), U4.2 (IN2)
unnamed: AE1.1 (A), C5.2, L1.2
unnamed: C6.2, L3.2, U1.2 (VDD3P3), U1.3 (VDD3P3)
unnamed: D1.2 (A), R1.2
unnamed: D2.2 (A), R2.2
unnamed: D3.2 (A), R3.2
unnamed: J1.1, U2.8 (OUT2)
unnamed: J1.2, U2.6 (OUT1)
unnamed: J2.1, U4.8 (OUT2)
unnamed: J2.2, U4.6 (OUT1)
unnamed: J5.A5 (CC1), R14.1
unnamed: J5.B5 (CC2), R15.1
unnamed: J5.A6 (D+), J5.B6 (D+), R13.2
unnamed: J5.A7 (D-), J5.B7 (D-), R12.1
unnamed: C18.1, R11.1, U1.7 (CHIP_EN)
unnamed: C4.2, L1.1, U1.1 (LNA_IN)
unnamed: C12.2, U1.29 (XTAL_N), X1.3 (OUT)
unnamed: L2.2, U1.30 (XTAL_P)
unnamed: R4.1, U2.7 (ISEN)
unnamed: R5.1, U4.7 (ISEN)
unnamed: C9.1, L2.1, X1.1 (EN)
PWM1: J6.1, U1.28 (U0TXD)
PWM2: J6.2, U1.27 (U0RXD)
PWM3: J8.1, U1.16 (GPIO10)
PWM4: J10.1, U1.13 (MTDO)
PWM5: J4.1, U1.4 (XTAL_32K_P)
PWM6: J4.2, U1.5 (XTAL_32K_N)
VUSB: C1.1, C2.1, J5.A4 (VBUS), J5.A9 (VBUS), J5.B4 (VBUS), J5.B9 (VBUS), J7.1, J9.1, U2.5 (VM), U3.1 (VIN), U3.2 (ON/OFF), U4.5 (VM)

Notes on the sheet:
THIS INDUCTOR IS NECESSARY TO SUPRESS RF HARMONICS
Logic Ground
High - Current Ground
Look up EEPROM storage for keeping channel values!
Impedance Matching for 2 layer board

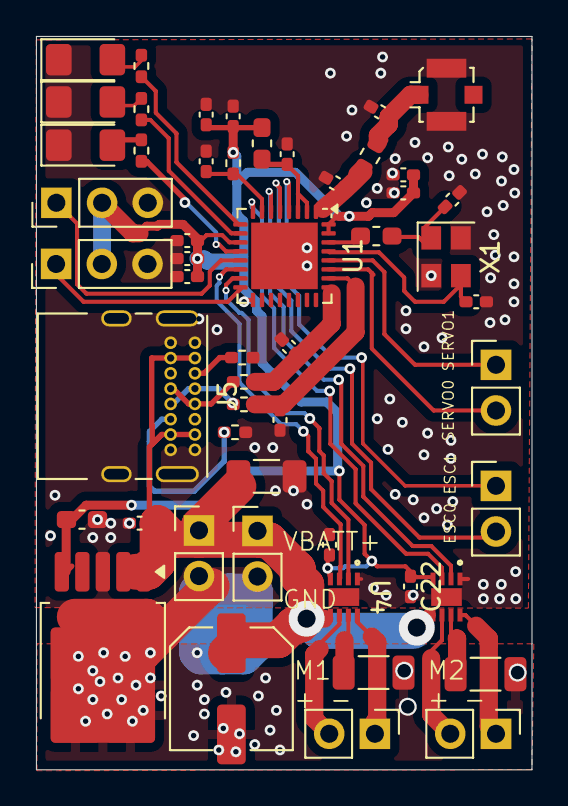
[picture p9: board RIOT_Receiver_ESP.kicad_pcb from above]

Board: 2 copper layers, 27.5 x 40.7 mm, 49 parts (0 on the bottom side), 38 nets.

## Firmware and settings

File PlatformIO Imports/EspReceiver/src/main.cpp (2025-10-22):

#include <Arduino.h>
#include <WiFi.h>
#include "EspNowEZ.h"
#include <esp_now.h>
#include <esp_system.h>
#include "esp_wifi.h"
#include <ESP32Servo.h>
#include <vector>
#include "ESC.h" // RC_ESP library installed by Library Manager

const uint8_t broadcastAddress[] = {0xFF, 0xFF, 0xFF, 0xFF, 0xFF, 0xFF};
int timeout = 0;
bool receivedRemoteSignal = false; 

#define Mot1 2
#define Mot2 3

#define Mot3 8
#define Mot4 9


#define ESC1 0
#define ESC2 1

//Servo library defaults from 20 to 180
#define ESCSMINDISTANCE 1000
#define ESCMAXDISTANCE 1900

#define SERVO1 10
#define SERVO2 7

#define SERVOIDLEANGLE 0
#define SERVOARMANGLE 90
#define SERVOATTACKANGLE 180

#define PWM1 20
#define PWM2 21

#define LED1 4
#define LED2 5
#define LED3 6


Servo FirstESC;
float escSpeed1 = 0;
ESC SecondESC(ESC2, 1000, 2000, 1000); 
uint16_t escSpeed2 = 0;
bool ESCArm[2] = {false, false};





//struct __attribute__((packed)) Message{
  const char id[20] = "Spenc";
//};



struct __attribute__((packed)) sendData{
    uint8_t macHandshake[6];
    uint8_t Direction[2]; // 0,1,2,3 FWD, BWD, Left, Right

    uint8_t DcMax[2] = {255,255};
    uint8_t DcMin[2] = {0,0};
    uint8_t dcMagnitude[2] = {0,0}; //Should be between 0 and 100
    bool objectArm[6]; // For escs, arm them, for servos, set to zero degrees? or fixable value
    bool objectRun[6]; 
    float escSpeed = .25; 

    bool connectCheck = false;
};

Container message;
uint8_t macAddress[6];
//Message msg;
sendData sD;
bool waitingForResponse(){

 

  //message.store(msg); 
  //message.printBytes();
  int result = esp_now_send(broadcastAddress, (uint8_t*) &id, sizeof(id) );
  //int result = ESPNow.broadcastMessage(message);
  result == ESP_OK ? digitalWrite(LED1, !digitalRead(LED1)) : digitalWrite(LED1, LOW);

  result == ESP_OK ? Serial.println("Sent successfully"): Serial.printf("Print failure %02x", ESP_OK);


  delay(250); // Send every 2 seconds


  return(true);

}

// Optional: callback for send status
//void onSend(const uint8_t *mac_addr, esp_now_send_status_t status) {

//}

void onReceive(const esp_now_recv_info *mac_info, const uint8_t *incomingData, int len) {
  const uint8_t *recv_info = mac_info->src_addr;
  
  if (len == sizeof(sendData)) {
    Serial.println("Data received from remote!"); 
    memcpy(&sD, incomingData, sizeof(sendData));

    //Serial.printf("%02x ,%02x,%02x,%20x: ", sD.Direction[0], sD.Direction[1], sD.objectRun[0], sD.objectArm[0]);
  //  for(size_t i= 0; i < len; i++){
  //    Serial.printf("%02X,", incomingData[i]);
  //  }
  //  Serial.printf("Length: %d", len);
  //  Serial.printf(": %d", sD.Direction[0]);
  //  Serial.println();

  //Serial.printf("Arm 0: %d, Arm 1: %d, Interact 0: %d, Interact 1: %d" , sD.objectArm[0],sD.objectArm[1], sD.objectRun[0], sD.objectRun[1] );
  //Serial.println();

    if (!esp_now_is_peer_exist(sD.macHandshake)) {
    Serial.println("Adding peer");
    ESPNow.add_peer(sD.macHandshake);
    }
    
    digitalWrite(LED2, HIGH);
    timeout = 1000;



    if(sD.macHandshake[5] == macAddress[5] && sD.macHandshake[4] == macAddress[4] && sD.macHandshake[3] == macAddress[3] ){
      digitalWrite(LED3, HIGH);
    }

  } else {
    Serial.print("Unexpected message length: ");
    Serial.println(len);
  }


}




void mapFunction(){
//  Serial.println("Mapping");

  if(sD.objectArm[0]){
    digitalWrite(LED3, HIGH);
    Serial.println("Arming");
    FirstESC.detach();

    //digitalWrite(ESC2, LOW);
    delay(100);
    FirstESC.attach(ESC2); // Send the Arm command to ESC
    FirstESC.writeMicroseconds(ESCSMINDISTANCE);


    ESCArm[0] = true;
    Serial.println("Done Arming");
  }

  if(ESCArm[0] && sD.objectRun[0]){
    
    if(escSpeed1 < (ESCMAXDISTANCE - ESCSMINDISTANCE)){ // Should be 7000
      escSpeed1+= sD.escSpeed;
    }

    FirstESC.writeMicroseconds(ESCSMINDISTANCE + int(escSpeed1) );
    digitalWrite(LED3, HIGH);
  }
  else if(!ESCArm[0]){
    //do nothing
  }
  else{
    digitalWrite(LED3, LOW);
    Serial.println("Stopping");
    if(escSpeed1 > 0){
      escSpeed1-=sD.escSpeed; 
    }
    FirstESC.writeMicroseconds(ESCSMINDISTANCE+ escSpeed1);
  }

  //Serial.printf("Max: %d : %d", sD.DcMax[0], sD.DcMax[1]);
  //Serial.println();

  //Serial.printf("Min: %d : %d", sD.DcMin[0], sD.DcMin[1]);
  //Serial.println();

  switch(sD.Direction[0]){
    case 0: // Stop
      analogWrite(Mot1, sD.DcMin[0]);
      analogWrite(Mot2, sD.DcMin[0]);
      analogWrite(Mot3, sD.DcMin[1]);
      analogWrite(Mot4, sD.DcMin[1]);
    break;
    case 1: // Forward
      analogWrite(Mot1, sD.DcMax[0]);
      analogWrite(Mot2, sD.DcMin[0]);
      analogWrite(Mot3, sD.DcMax[1]);
      analogWrite(Mot4, sD.DcMin[1]);
    break;
    case 2: // Backward
      analogWrite(Mot1, sD.DcMin[0]);
      analogWrite(Mot2, sD.DcMax[0]);
      analogWrite(Mot3, sD.DcMin[1]);
      analogWrite(Mot4, sD.DcMax[1]);
    break;
    case 3: // Left
      analogWrite(Mot1, sD.DcMin[0]);
      analogWrite(Mot2, sD.DcMax[0]);
      analogWrite(Mot3, sD.DcMax[1]);
      analogWrite(Mot4, sD.DcMin[1]);
    break;
    case 4: // Right
      analogWrite(Mot1, sD.DcMax[0]);
      digitalWrite(Mot2, sD.DcMin[0]);
      digitalWrite(Mot3, sD.DcMin[1]);
      analogWrite(Mot4, sD.DcMax[1]);
    break;
    default:
      analogWrite(Mot1, sD.DcMin[0]);
      analogWrite(Mot2, sD.DcMin[0]);
      analogWrite(Mot3, sD.DcMin[1]);
      analogWrite(Mot4, sD.DcMin[1]);
    break;

  };


}

void setup() {
//  delay(10000);
  Serial.begin(115200);
 // delay(1000);

  //delay(250);

  pinMode(Mot1, OUTPUT);
  pinMode(Mot2, OUTPUT);
  pinMode(Mot3, OUTPUT);
  pinMode(Mot4, OUTPUT);
  pinMode(LED1, OUTPUT);
  pinMode(LED2, OUTPUT);
  pinMode(LED3, OUTPUT);

//  pinMode(ESC1, OUTPUT);
 // pinMode(ESC2, OUTPUT);   

  digitalWrite(LED1,LOW);
  digitalWrite(LED2, LOW);
  digitalWrite(LED3, LOW);

  digitalWrite(Mot1, LOW);
  digitalWrite(Mot2, LOW);
  digitalWrite(Mot3, LOW);
  digitalWrite(Mot4, LOW);



  //ESP_ERROR_CHECK(esp_wifi_set_channel(chan,WIFI_SECOND_CHAN_NONE));

  WiFi.mode(WIFI_MODE_STA);
  WiFi.disconnect();
  ESPNow.init();
  WiFi.macAddress(macAddress); 
  WiFi.setTxPower(WIFI_POWER_19dBm);
  ESPNow.reg_recv_cb(onReceive);
  // Optional: set send callback if you want to track status
  //ESPNow.reg_send_cb(onSend);

  
  Serial.print("My MAC Address: ");
  Serial.printf("%02x:%02x:%02x:%02x:%02x:%02x", macAddress[0],macAddress[1],macAddress[2],macAddress[3],macAddress[4],macAddress[5]);


  // Initialize ESP-NOW
  if (esp_now_init() != ESP_OK) {
    Serial.println("Error initializing ESP-NOW");
    return;
  }
  ESPNow.add_peer((uint8_t*)broadcastAddress,0); 

}

void loop() {
  if(timeout > 0){
    digitalWrite(LED1, LOW);
    mapFunction();
    timeout--;
    delay(10);
  }
  else{
    digitalWrite(LED1,LOW);
    digitalWrite(LED2, LOW);
    waitingForResponse();
  }

}

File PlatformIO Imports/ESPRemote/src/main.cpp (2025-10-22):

//#include <U8g2lib.h>
#include <Arduino.h>
#include "EspNowEZ.h"
#include "u8g2EZ.h"
#include <esp_event.h>
#include "esp_event_base.h"
#include <GPIOControl.h>
#include <math.h>
#include <WiFi.h>
#include <esp_wifi.h>
#include <esp_now.h>
#include <vector>
#include <string>
//#include <WiFi.h>



// Loop function

    // Structure to receive incoming messages
    //struct __attribute__((packed)) Message{
     
    //};

    struct __attribute__((packed)) sendData{
    uint8_t macHandshake[6];
    uint8_t Direction[2]; // 0,1,2,3 FWD, BWD, Left, Right

    uint8_t DcMax[2] = {125,125};
    uint8_t DcMin[2] = {0,0};
    uint8_t dcMagnitude[2] = {0,0}; //Should be between 0 and 100
    bool objectArm[6]; // For escs, arm them, for servos, set to zero degrees? or fixable value
    bool objectRun[6]; 
    float escSpeed = .25; 

    bool connectCheck = false;
};

    struct activeRecivers{
        std::string name; // left and right, 1 and 2
        uint8_t mac[6];

        //Constructor copies the name and mac bytes
        activeRecivers(const std::string& n, const uint8_t* m) : name(n) {
            memcpy(mac, m, 6);
        }
    };

sendData sD;
Container c;
//Message bC;

std::vector<activeRecivers*> foundReceivers;
activeRecivers *selectedReciver = nullptr;


enum ButtonGPIO{
    LEFTTRIGGER = 7, //10, 20, 21, 7
    RIGHTTRIGGER = 21,
    BOTTOMBUTTON  = 20,
    TOPBUTTON = 10,


};


const uint8_t buttonsGPIO[4] = {LEFTTRIGGER,RIGHTTRIGGER,BOTTOMBUTTON,TOPBUTTON};
const uint8_t analogGPIO[4] = {1,2,3,4};

uint8_t SDAPIN = 8;
uint8_t SCLPIN = 9;

enum Direction {
    STOP = 0,
    FORWARD = 1,
    BACKWARD = 2,
    LEFT = 3,
    RIGHT = 4,
    

};



pinData pd; 


int count = 0;
const int SELECTIONLIST =  2;
double rLeft, theta_degLeft;
double rRight, theta_degRight;

void joystickToPolarLeft(uint16_t x, uint16_t y){
    int16_t xCentered = x - 2048;
    int16_t yCentered = y - 2048;

    rLeft = sqrt((xCentered * xCentered) + (yCentered  * yCentered));
    theta_degLeft = (atan2(yCentered,xCentered)) * (180/3.14);

    if(theta_degLeft < 0){
        theta_degLeft = 360 + theta_degLeft;
    }
}

void joystickToPolarRight(uint16_t x, uint16_t y){
    int16_t xCentered = x - 2048;
    int16_t yCentered = y - 2048;

    rRight = sqrt((xCentered * xCentered) + (yCentered  * yCentered));
    theta_degRight = (atan2(yCentered,xCentered)) * (180/3.14);

    if(theta_degRight < 0){
        theta_degRight = 360 + theta_degRight;
    }
}

/*###########################WIRELESS FUNCTIONS ###############################*/
void onRecv(const esp_now_recv_info *mac_info, const uint8_t *data, int data_len) {
        char id[20];
    const uint8_t *mac_addr = mac_info->src_addr;
    if (data_len == sizeof(id) ){
        memcpy(&id, data, sizeof(id));
    char macStr[18];
    snprintf(macStr, sizeof(macStr), "%02x:%02x:%02x:%02x:%02x:%02x",
             mac_addr[0], mac_addr[1], mac_addr[2], mac_addr[3], mac_addr[4],
             mac_addr[5]);
    //Serial.print("Last Packet Recv from: ");
    //Serial.println(macStr);

    /*
    Serial.print("Incoming Message: ");
    for(int i = 0; i < data_len; i++){
        Serial.printf("%02X ", data[i]);
    }
    Serial.print(" : ");
    Serial.print(id);
    Serial.println(); 
    */
    bool inList = false;
    for (auto receiver : foundReceivers){
        if(receiver->name == id){
             inList = true; 
        }

    }

    if(!inList){
        foundReceivers.push_back(new activeRecivers(id, mac_addr));
    }

  } else {
    Serial.print("Unexpected message length: ");
    Serial.println(data_len);
  }


}

void doMath(pinData p){ // convert button presses

// joystick 1 should control the movement

//button 2 will control the esc
    sD.objectArm[0] = p.buttons[0];
    sD.objectArm[1] = p.buttons[0];

    sD.objectArm[2] = p.buttons[1];
    sD.objectArm[3] = p.buttons[1];

    sD.objectRun[2] = p.buttons[2];
    sD.objectRun[3] = p.buttons[2];

    sD.objectRun[0] = p.buttons[3];
    sD.objectRun[1] = p.buttons[3];



    joystickToPolarLeft(p.joysticks[0], p.joysticks[1]);
    joystickToPolarRight(p.joysticks[2], p.joysticks[3]);

    if(rLeft < 1500){
    sD.Direction[0] = 0; // Stop
    sD.dcMagnitude[0] = 0;
    } else{
        if(theta_degLeft < 45 || theta_degLeft >= 315 ){
            sD.Direction[0] = 3; // Move left
        }
        else if(theta_degLeft >= 45 && theta_degLeft < 135){
            sD.Direction[0] = 1; // Move forward 
        }
        else if(theta_degLeft >= 135 && theta_degLeft < 225){
            sD.Direction[0] = 4; // Move right
        }
        else if(theta_degLeft >= 225 && theta_degLeft < 315){
            sD.Direction[0] = 2; // Move backward
        }
        sD.dcMagnitude[0] = 100;
    }
    if(rRight < 1500){
    sD.Direction[1] = 0; // Stop
    sD.dcMagnitude[1] = 0;
    } else{
        if(theta_degRight < 45 || theta_degRight >= 315 ){
            sD.Direction[1] = 3; // Move left
        }
        else if(theta_degRight >= 45 && theta_degRight < 135){
            sD.Direction[1] = 1; // Move forward 
        }
        else if(theta_degRight >= 135 && theta_degRight < 225){
            sD.Direction[1] = 4; // Move right
        }
        else if(theta_degRight >= 225 && theta_degRight < 315){
            sD.Direction[1] = 2; // Move backward
        }
        sD.dcMagnitude[1] = 100;
    }




}

//Joystick1 x = 1, y = 0
//Joystick2 x = 2, y = 3

//Top left trigger = 4
// Top right tigger = 5
//Bottom bottom = 6
//Top right = 7



void setup(){

Serial.begin(115200);
//Serial.println("Staring Code:");
U8G2EZ_init();


//u8g2.clearBuffer();
//drawSimple("Searching for Receivers...", 3000, 0, 30, true);

//Serial.println("Pressing Buttons:");
inputPinsSetup(buttonsGPIO);
inputPinsSetup(analogGPIO);

WiFi.mode(WIFI_MODE_STA);
//WiFi.disconnect();
ESPNow.init();
ESPNow.reg_recv_cb(onRecv);

int selection = 0;
int max = SELECTIONLIST;
int min = 0;
//foundReceivers.reserve(10);
// Menu to select the reciver. Revise for later.
//uint8_t test1_mac[6] = {00,00,00,00,00,0};
//oundReceivers.push_back(new activeRecivers("Test 1", test1_mac)); // Temporary line to simulate found receivers

//delay(1000);
//uint8_t test2_mac[6] = {12,34,56,78,90,0};
//foundReceivers.push_back(new activeRecivers("Test 2", test2_mac)); // Temporary line to simulate found receivers
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
